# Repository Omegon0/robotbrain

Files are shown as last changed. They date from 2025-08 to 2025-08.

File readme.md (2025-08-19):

# ROBOTBRAIN

An ESP32-based robot board that integrates two L293DD ICs to control four DC motor outputs. Also has an integrated magnetometer (LIS3MDL) for direction control. 

## Why? 

Last year for Science Olympiad's Robot Tour event, I designed an omnidirectional robot with tons of features, and importantly, many of them were based on QFN packages and a very weak LDO. 
This time I'm doing better. 5A LDO. No QFN (except the magnetometer). Proper power regulation. 
This will be the better robot. 

## What's changed? 

The previous version also contained a LSM6DSOX IC which has been scrapped since the SciOly robot can't effectively use linear and rotational acceleration data (too much drift). However magnetic field helps with absolute positioning. 
The previous version used a 1A LDO which was too little for three motors. This uses a 5A LDO which is plenty for 4 motors. The motor drivers have been upgraded to large L293DD packages to account for the higher current load. 
The power switching system has been significantly simplified, using a physical switch to alternate between battery power and USB power. There is no integrated battery charging since the robot is designed to use 8xAA (12V) instead of a 3.7V LiPo. 
Has an extra button to calibrate and start the robot because it may be easier than resetting. can be used to toggle on/off instead of robot running every time code uploads. 

## Images

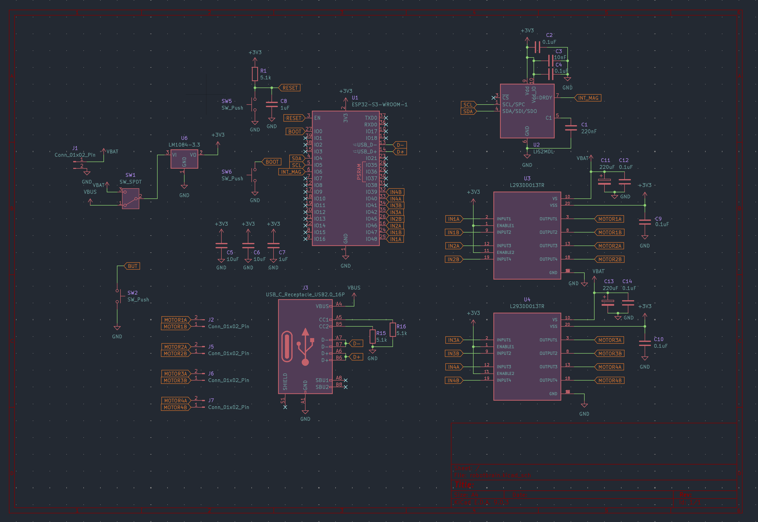
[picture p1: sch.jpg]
sch

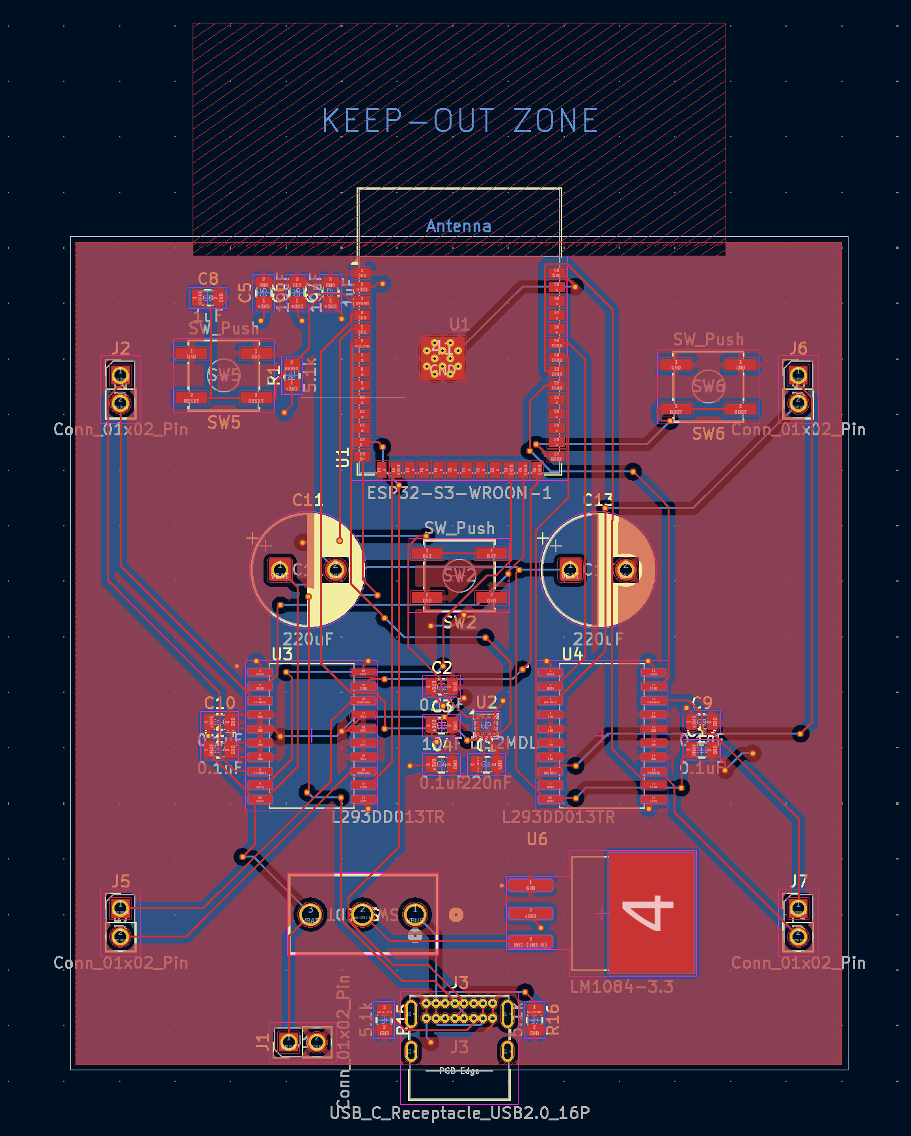
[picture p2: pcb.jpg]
pcb

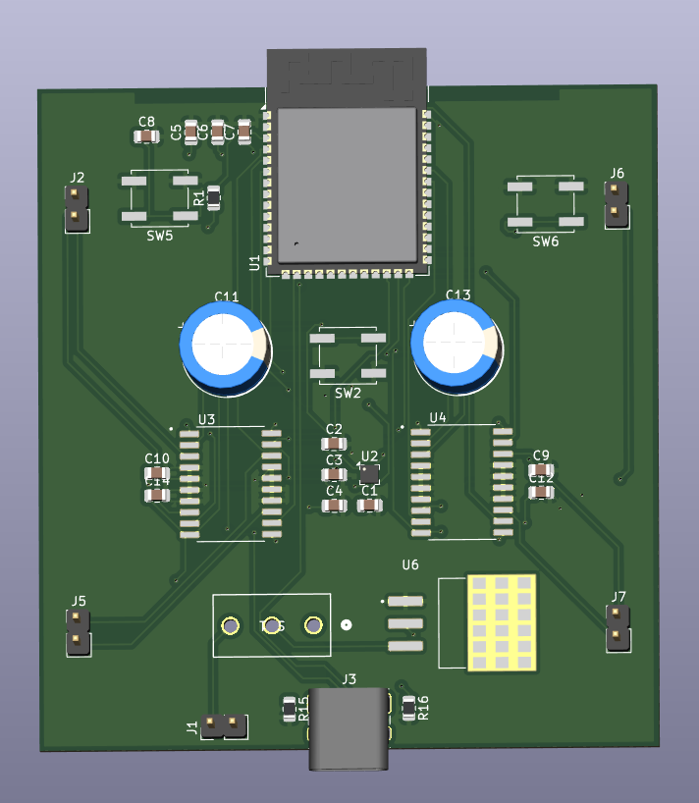
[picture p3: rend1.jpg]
rend1

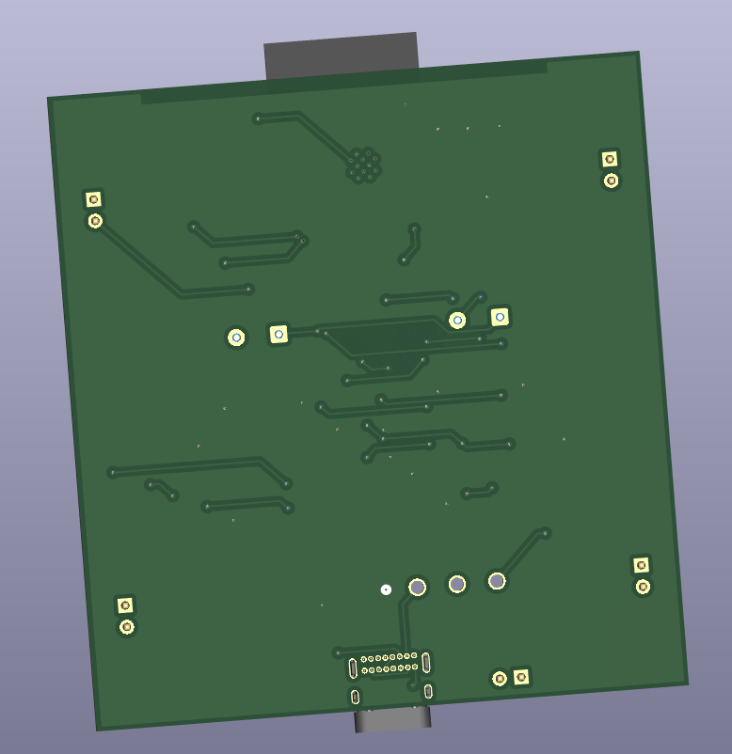
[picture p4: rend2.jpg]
rend2


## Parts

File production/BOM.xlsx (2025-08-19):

Comment | Designator | Footprint | JLCPCB Part #（optional）
ST L293DD013TR | U3,U4 | SOIC127P1032X265-20N | C21610
ST LIS3MDLTR | U2 | LGA-12_2x2mm_P0.5mm | C478483
ESPRESSIF ESP32-S3-WROOM-1-N8 | U1 | ESP32-S3-WROOM-1 | C2913198
HGSEMI LM1084IS-3.3/TR | U6 | TO254P1524X483-4N | C19193518
220uF | C11,C13 | C_0805_2012Metric | C233093
220nF | C1 | C_0805_2012Metric | C48579621
100nF | C2,C4,C9,C10,C12,C14 | C_0805_2012Metric | C49326703
10nF | C3 | C_0805_2012Metric | C48579597
1uF | C7 | C_0805_2012Metric | C28323
10uF | C5,C6,C7 | C_0805_2012Metric | C48579582
USB C | J3 | USB_C_Receptacle_GCT_USB4085 | C7095263
SPDT | SW1 | SS-12D10G5_XKB | C319013
5.1k | R1,R15,R16 | R_0805_2012Metric | C27834

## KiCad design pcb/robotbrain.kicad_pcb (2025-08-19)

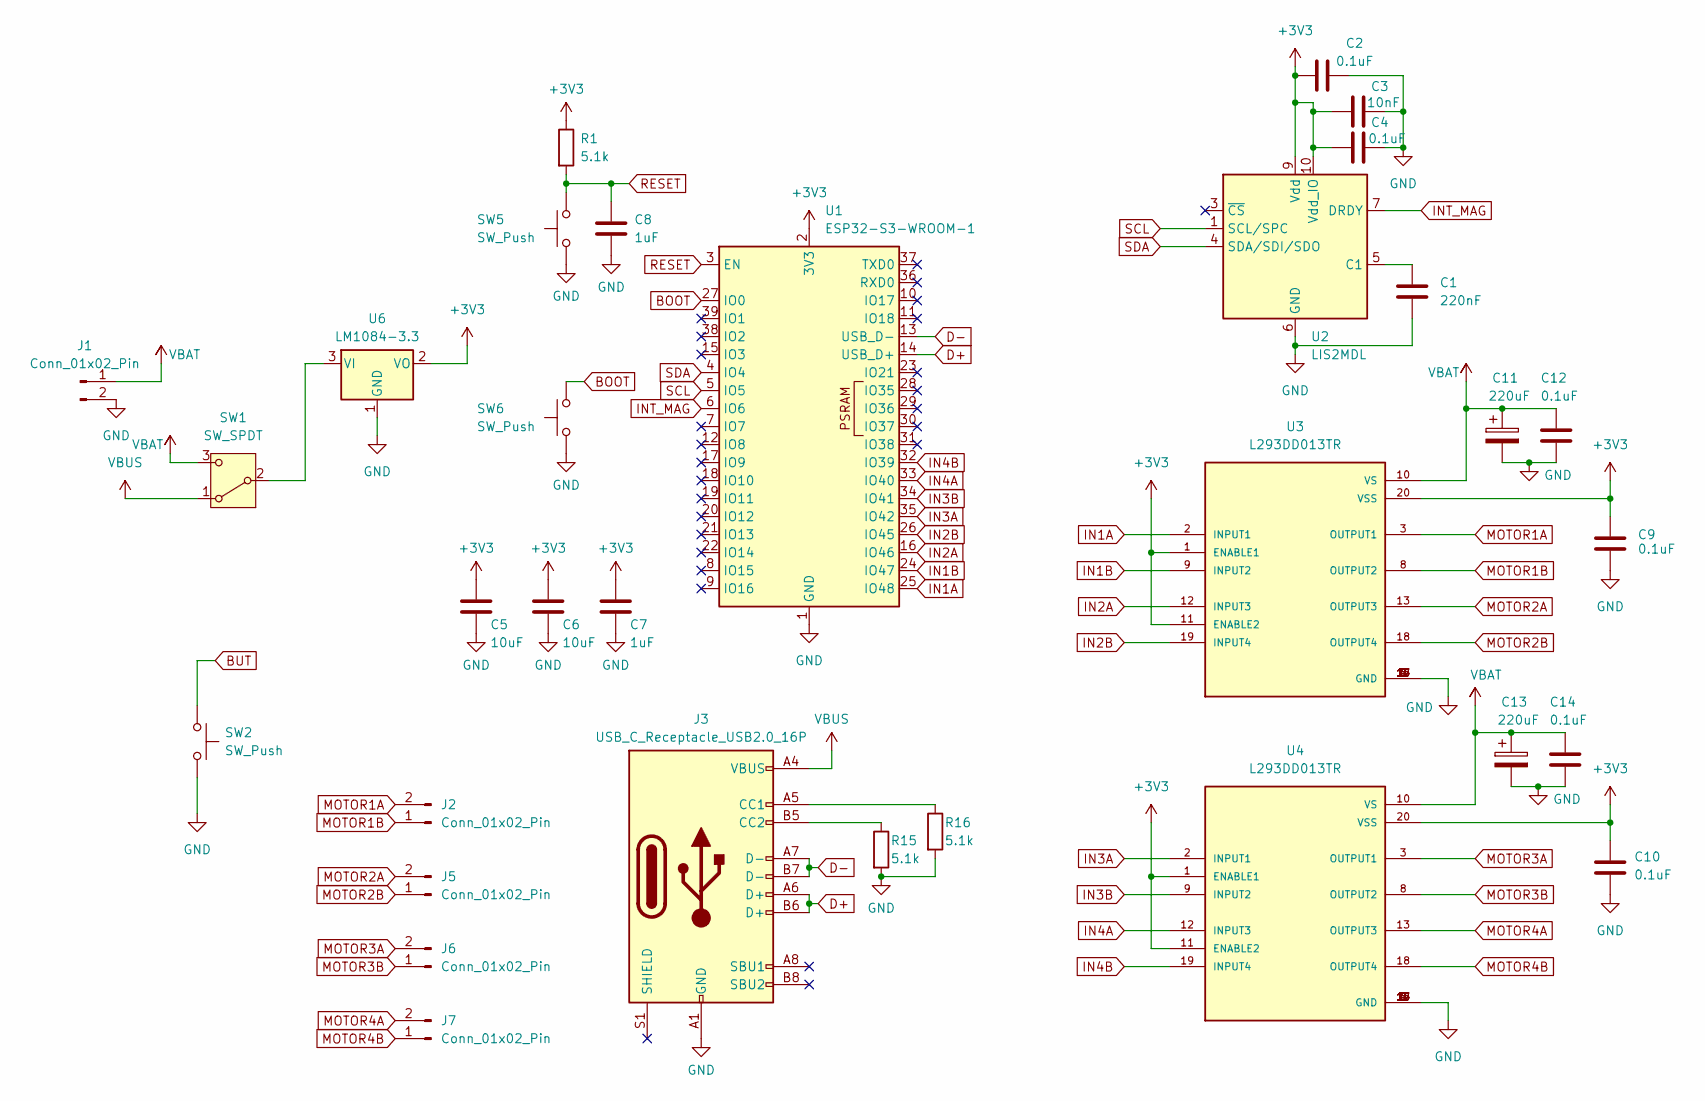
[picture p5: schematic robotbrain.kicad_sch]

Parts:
C1: 220nF; C_0805_2012Metric
C2, C4, C9, C10, C12, C14: 0.1uF; C_0805_2012Metric
C3: 10nF; C_0805_2012Metric
C5, C6: 10uF; C_0805_2012Metric
C7, C8: 1uF; C_0805_2012Metric
C11, C13: 220uF; CP_Radial_D10.0mm_P5.00mm
J1, J2, J5, J6, J7: Conn_01x02_Pin; PinHeader_1x02_P2.54mm_Vertical
J3: USB_C_Receptacle_USB2.0_16P; USB_C_Receptacle_GCT_USB4085
R1, R15, R16: 5.1k; R_0805_2012Metric
SW1: SW_SPDT; SS-12D10G5_XKB
SW2, SW5, SW6: SW_Push; SW_Push_1P1T_NO_CK_KSC6xxJ
U1: ESP32-S3-WROOM-1
U2: LIS2MDL; LGA-12_2x2mm_P0.5mm
U3, U4: L293DD013TR; SOIC127P1032X265-20N
U6: LM1084-3.3; TO254P1524X483-4N

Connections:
+3V3: C2.1, C3.1, C4.1, C5.1, C6.1, C7.1, C9.1, C10.1, R1.1, U1.2 (3V3), U2.9 (Vdd), U2.10 (Vdd_IO), U3.1 (ENABLE1), U3.11 (ENABLE2), U3.20 (VSS), U4.1 (ENABLE1), U4.11 (ENABLE2), U4.20 (VSS), U6.2 (VO)
BOOT: SW6.2, U1.27 (IO0)
BUT: SW2.1
D+: J3.A6 (D+), J3.B6 (D+), U1.14 (USB_D+)
D-: J3.A7 (D-), J3.B7 (D-), U1.13 (USB_D-)
GND: C1.2, C2.2, C3.2, C4.2, C5.2, C6.2, C7.2, C8.2, C9.2, C10.2, C11.2, C12.2, C13.2, C14.2, J1.2, J3.A1 (GND), J3.A12 (GND), J3.B1 (GND), J3.B12 (GND), R15.2, R16.2, SW2.2, SW5.1, SW6.1, U1.1 (GND), U1.40 (GND), U1.41 (GND), U2.6 (GND), U2.8 (GND), U3.4 (GND), U3.5 (GND), U3.6 (GND), U3.7 (GND), U3.14 (GND), U3.15 (GND), U3.16 (GND), U3.17 (GND), U4.4 (GND), U4.5 (GND), U4.6 (GND), U4.7 (GND), U4.14 (GND), U4.15 (GND), U4.16 (GND), U4.17 (GND), U6.1 (GND)
IN1A: U1.25 (IO48), U3.2 (INPUT1)
IN1B: U1.24 (IO47), U3.9 (INPUT2)
IN2A: U1.16 (IO46), U3.12 (INPUT3)
IN2B: U1.26 (IO45), U3.19 (INPUT4)
IN3A: U1.35 (IO42), U4.2 (INPUT1)
IN3B: U1.34 (IO41), U4.9 (INPUT2)
IN4A: U1.33 (IO40), U4.12 (INPUT3)
IN4B: U1.32 (IO39), U4.19 (INPUT4)
INT_MAG: U1.6 (IO6), U2.7 (DRDY)
MOTOR1A: J2.2, U3.3 (OUTPUT1)
MOTOR1B: J2.1, U3.8 (OUTPUT2)
MOTOR2A: J5.2, U3.13 (OUTPUT3)
MOTOR2B: J5.1, U3.18 (OUTPUT4)
MOTOR3A: J6.2, U4.3 (OUTPUT1)
MOTOR3B: J6.1, U4.8 (OUTPUT2)
MOTOR4A: J7.2, U4.13 (OUTPUT3)
MOTOR4B: J7.1, U4.18 (OUTPUT4)
unnamed: J3.A5 (CC1), R16.1
unnamed: J3.B5 (CC2), R15.1
unnamed: SW1.2 (B), U6.3 (VI)
unnamed: C1.1, U2.5 (C1)
RESET: C8.1, R1.2, SW5.2, U1.3 (EN)
SCL: U1.5 (IO5), U2.1 (SCL/SPC)
SDA: U1.4 (IO4), U2.4 (SDA/SDI/SDO)
VBAT: C11.1, C12.1, C13.1, C14.1, J1.1, SW1.3 (C), U3.10 (VS), U4.10 (VS)
VBUS: J3.A4 (VBUS), J3.A9 (VBUS), J3.B4 (VBUS), J3.B9 (VBUS), SW1.1 (A)

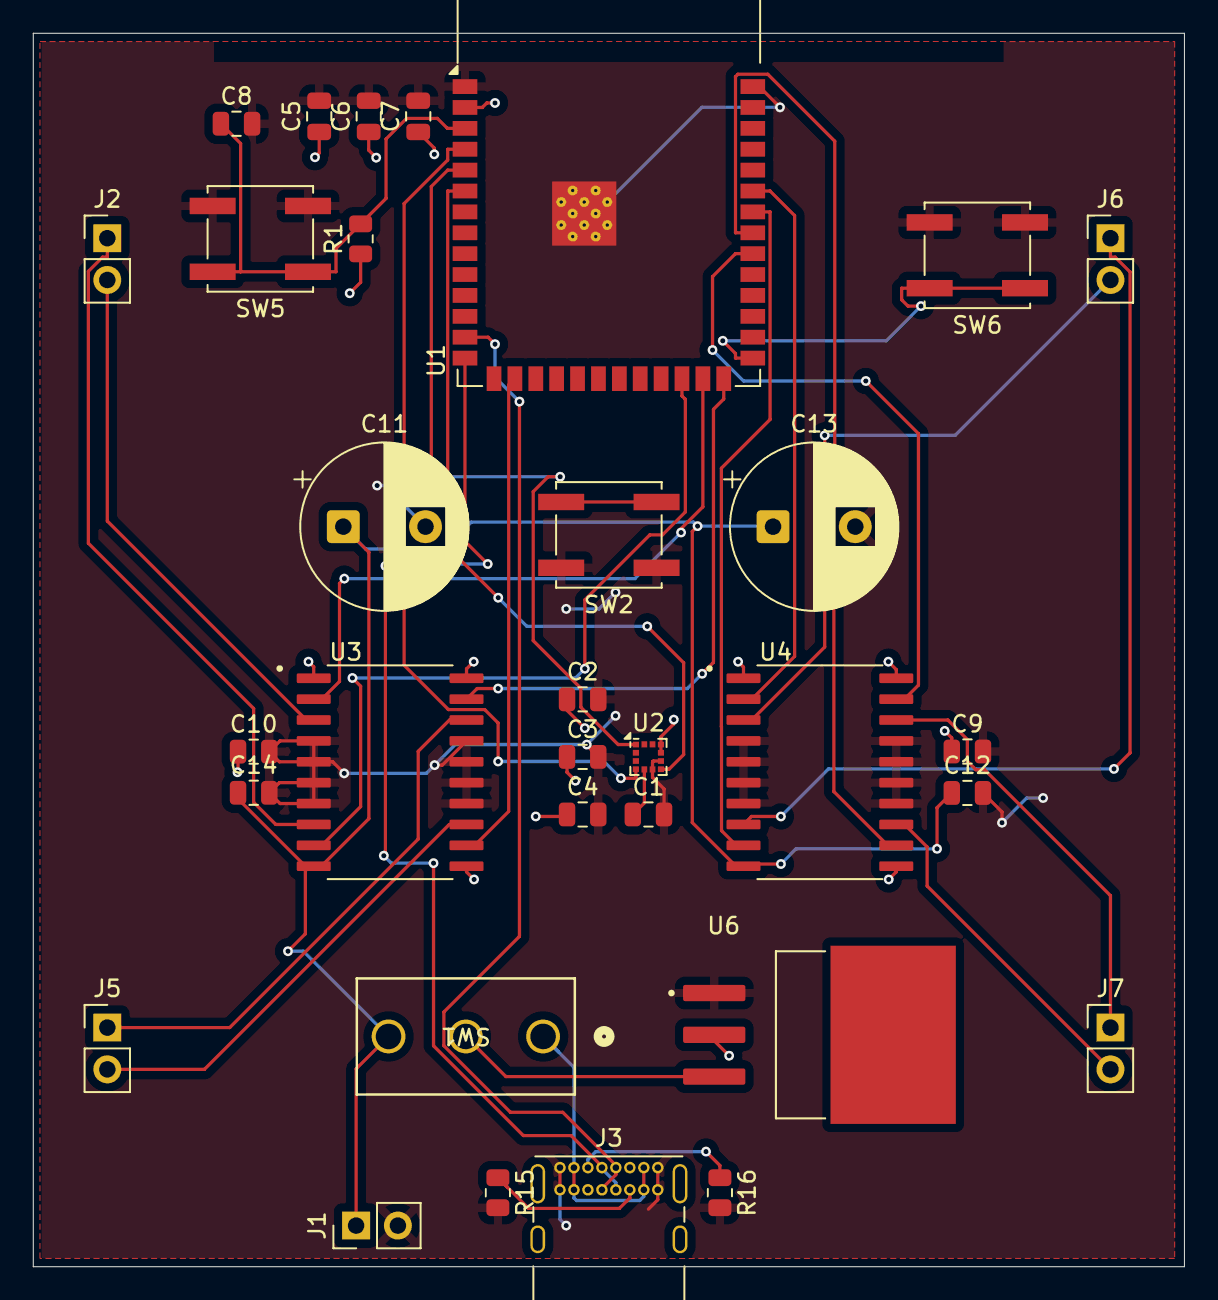
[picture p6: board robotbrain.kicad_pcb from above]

Board: 2 copper layers, 70.0 x 75.0 mm, 32 parts (0 on the bottom side), 31 nets.

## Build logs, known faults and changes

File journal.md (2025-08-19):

---
Title: "Robot Brain"
Author: "Padimo/Omegon0"
Description: "Upgraded ESP32-based robot circuit board."
Created On: "8/8/2025"
---

# Day 1 8/8

This is the second attempt of making a robot. The first attempt failed because I tried to hotplate a lot of QFN packages and legitimately the only parts that worked were USB power, ESP and a singular neopixel. 
This attempt aims to simplify the robot so that it actually works. 

First of all motors need a decent amount of current so I'm using the LM1084-3v3 to supply that. (tbh doesn't really matter since the H bridges will be supplied from 12V battery but just in case)
H bridges I want an SMD equivalent of an L293N

Found one its called the L293DD and it has lots of ground pads. i think that's for heat sucking so that's important
started schematic 
For USB/battery power switching I'm just gonna use a physical slide switch SPDT because I cannot be bothered to create an automatic switching circuit (the last one failed miserably, see the EMG project)
wired a bit of stuff up

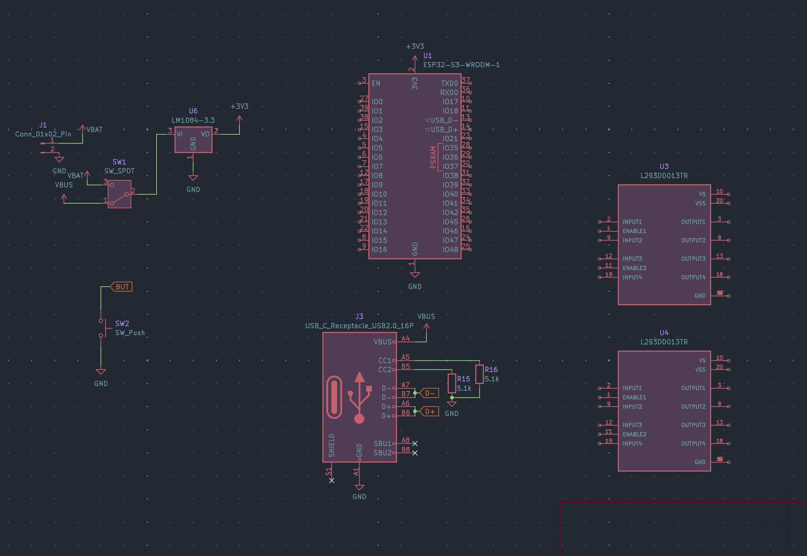
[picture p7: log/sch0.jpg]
sch0


*time spent: 2h*

# Day 2 8/9

Wired up the motor drivers. 
I decided to add a magnetometer LIS2MDL because magnetic fields are a good way of measuring direction (compass)
I hate datasheets. I had to add electrolytic caps for the motor drivers and those are THT. Don't know if JLC PCBA will do that

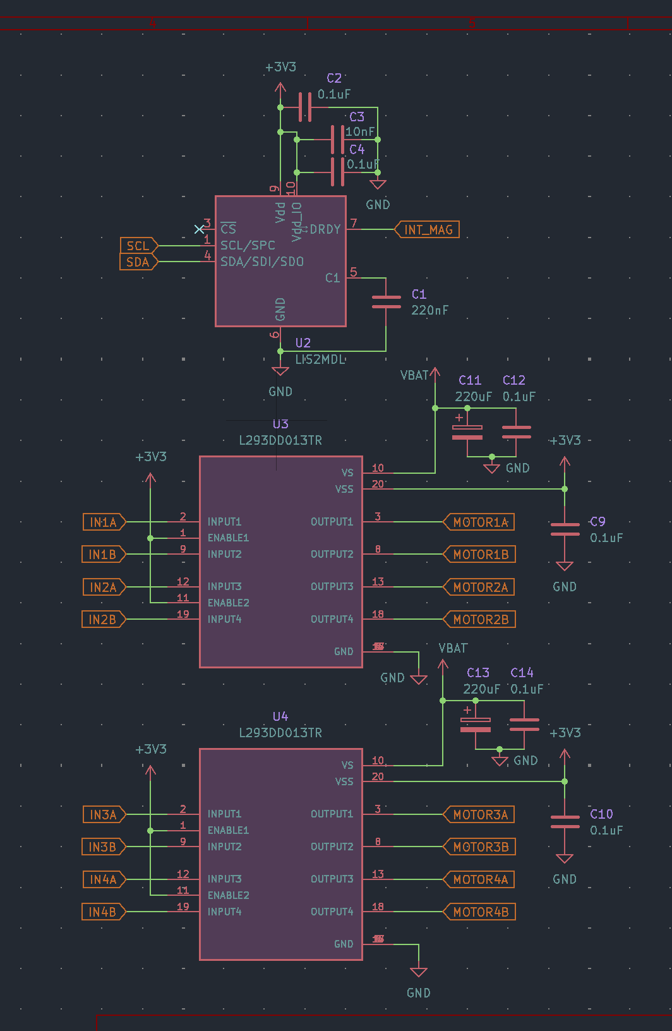
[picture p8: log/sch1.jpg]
sch1


*time spent: 3h*

# Day 3 8/10

Wired up the ESP. Added footprints

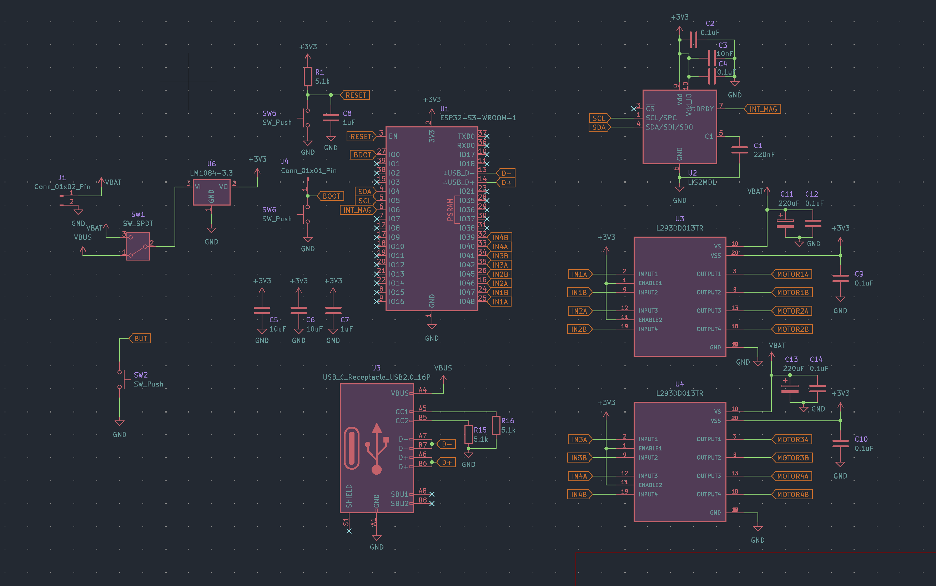
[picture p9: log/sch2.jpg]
sch2


*time spent: 2h*

# Day 4 8/13

I realize now that the USB port is also THT, whoops. Well LCSC has it so I'm using it, I may have to hand-solder those items later on. Can't avoid PCBA because LIS2MDL. 
Arranged PCB outline and board (no image i forgot whoops)
how have i done so many PCB projects and not known about align/distribute. feels like a crime

*time spent: 2h*

# Day 5 8/14

I hand routed the whole board then realized I had no zones. Added those and then redid the board. only THEN did I google automatic routing kicad and install the freerouting plugin

pcb

*time spent: 3h*

# Day 6 8/15

Created github and stuff and wrote this journal based off of my own logs (i used my zip extension! check out https://github.com/Omegon0/zip)
Created renders and added some components (many steps failed to load. still working on that)

*time spent: 2h*

# Day 7 8/19

submitting today! 
edit: forgot to actually commit to and push the repo. i just said i dumped everything

created all production files

*time spent: 3h*

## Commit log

2025-08-19 dump everything
    [robotbrain-B_Cu.gbr, robotbrain-B_Mask.gbr, robotbrain-B_Paste.gbr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]
2025-08-19 added production files
    [BOM.xlsx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]
